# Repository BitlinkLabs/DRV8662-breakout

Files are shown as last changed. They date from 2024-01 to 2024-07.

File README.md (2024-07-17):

# DRV8662-breakout

<p align="center">
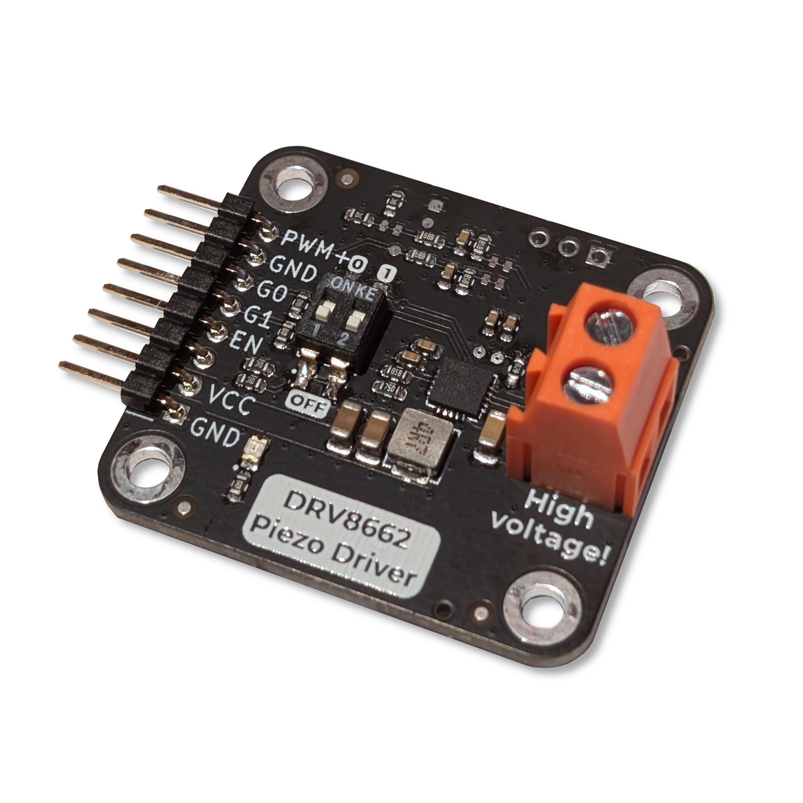
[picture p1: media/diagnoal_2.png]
  
&nbsp; &nbsp; &nbsp; &nbsp;
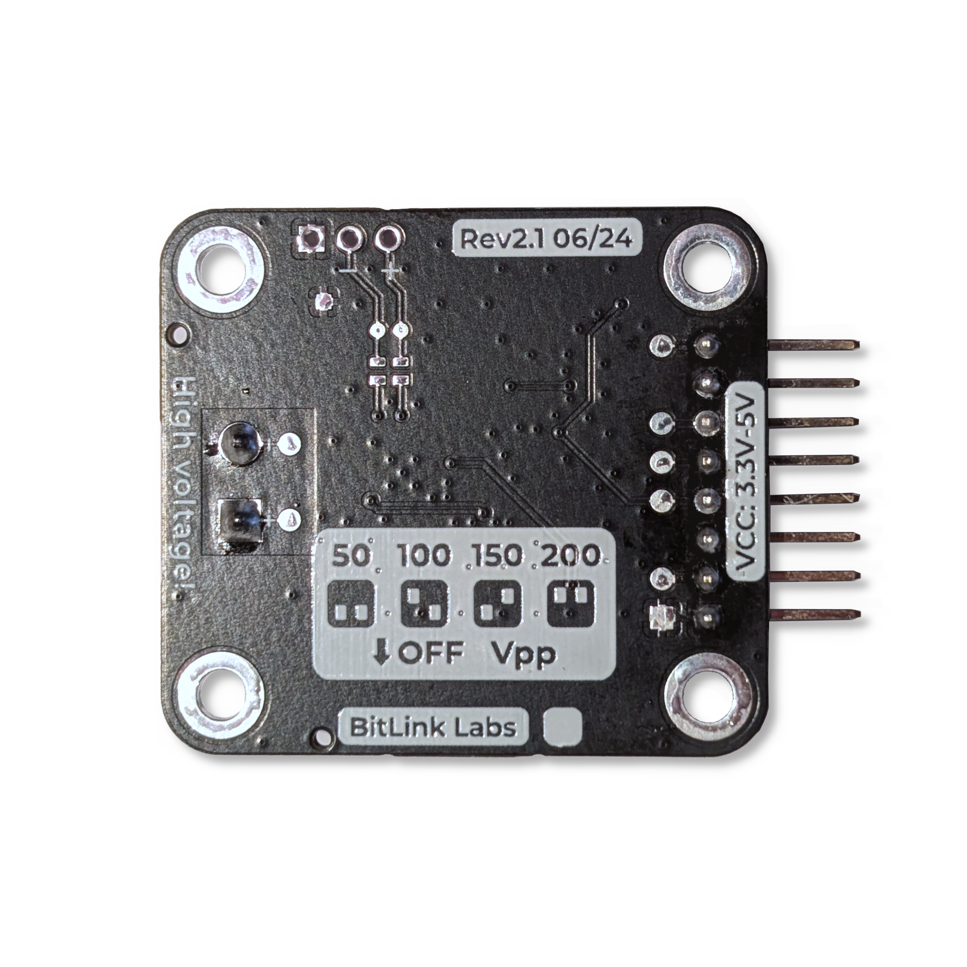
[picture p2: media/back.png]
  
&nbsp; &nbsp; &nbsp; &nbsp;
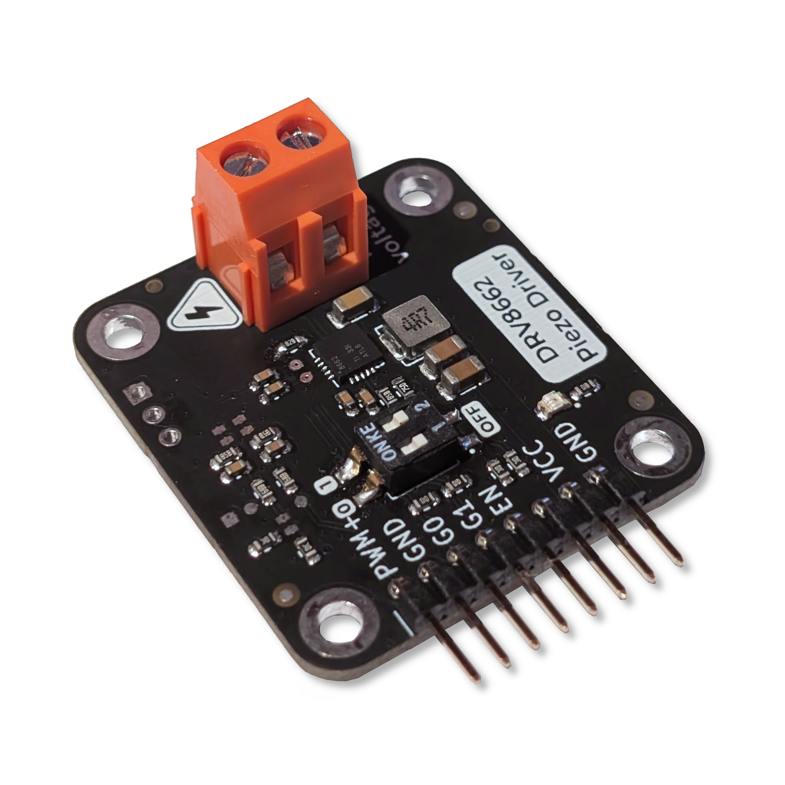
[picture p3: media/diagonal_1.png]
Dark
  
</p>

### What is it?
This is a ready-to-go development board with everything necessary to run piezo actuators.
It features a DRV8662 IC from Texas Instruments and all the additional circuitry for it to work as expected.

### How does it function?
The IC serves multiple purposes. First of all it is a boost-converter to generate up 200V from the 3.3-5V it takes as an input. Secondly it features an amplifier which takes a PWM Signal and drives the Output pins to the respective differential values according to the input.

At the output you can connect a piezo actuator for haptic feedback or valves & pumps.
The output voltage is an AC Waveform with an adjustable Peak-to-Peak voltage.

### What is special about it?
The Output voltage can be to 4 approximate values: 50Vpp, 100Vpp, 150Vpp, 200Vpp using a simple dip switch.

### How do I get started?
All you need to do is connect an PWM and GND pin of a microcontroller to the PWM+ Pin and GND pin of the development board respectively. This covers the “signal” part.
To power the dev board you can either use the USB mini jack (we recommend using a USB hub for this) or through the included VCC and GND Pins. 
Be sure to stick to an input voltage of 3.3V to 5V and be aware that the USB voltage will be present on the VCC pin.



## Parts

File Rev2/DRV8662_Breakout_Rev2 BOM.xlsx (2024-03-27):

DRV 8662 Breakout Rev2 |  |  |  |  |  |  |  | (Stand 27.03.24)
Ref | Description | Qnty | Value | Cmp name | Footprint | VoltageRating | ManuNumber | LCSC Part Number | Stock | Link | Datasheet
C1, C2, C5, C6, C7, C8, |  | 6 | 100nF | C_Small | Capacitor_SMD:C_0603_1608Metric |  |  | C14663 | At home | https://jlcpcb.com/partdetail/Yageo-CC0603KRX7R9BB104/C14663 | ~
C3, | 250V Boost cap. | 1 | 100nF | C_Small | Capacitor_SMD:C_1206_3216Metric |  |  | C346235 |  | https://www.lcsc.com/product-detail/Multilayer-Ceramic-Capacitors-MLCC-SMD-SMT_Samsung-Electro-Mechanics-CL31B104KEHNNNE_C346235.html | ~
C9, C10, |  | 2 | 10uF | C | Capacitor_SMD:C_1206_3216Metric |  |  | C13585 |  | https://www.lcsc.com/product-detail/Multilayer-Ceramic-Capacitors-MLCC-SMD-SMT_Samsung-Electro-Mechanics-CL31A106KBHNNNE_C13585.html | ~
D1, |  | 1 | LED_Small | LED_Small | LED_SMD:LED_0805_2012Metric |  |  |  | At home |  | ~
J1, |  | 1 | Conn_IO | Conn_01x08 | MAINTECH_Connectors:PinHeader_1x08_P2.54mm_Horizontal_withSmdPads |  |  |  | At home |  | ~
J2, | Orange screw terminal | 1 | Conn_Screw | Screw_Terminal_01x02 | MAINTECH_Connectors:DB128L-5.08-2P |  |  | C430603 |  | https://www.lcsc.com/product-detail/Screw-terminal_DORABO-DB128L-5-08-2P-OG-S_C430603.html | ~
L1, | Inductor | 1 | 4.7uH | L | MAINTECH_Passives:Inductor_FXL0420-4R7-M |  | FXL0420-4R7-M | C167208 |  | https://www.lcsc.com/product-detail/Power-Inductors_cjiang-Changjiang-Microelectronics-Tech-FXL0420-4R7-M_C167208.html | ~
R1, R6, R7, R16, |  | 4 | 10k | R_Small | Resistor_SMD:R_0603_1608Metric |  |  | C25804 | At home | https://jlcpcb.com/partdetail/26547-0603WAF1002T5E/C25804 | ~
R14, R15, |  | 2 | 100k | R_Small | Resistor_SMD:R_0603_1608Metric
R2, |  | 1 | 6.98k | R_Small | Resistor_SMD:R_0603_1608Metric_Pad0.98x0.95mm_HandSolder |  |  | C862806 |  | https://www.lcsc.com/product-detail/Chip-Resistor-Surface-Mount_YAGEO-RT0603DRD076K98L_C862806.html | ~
R3, |  | 1 | 590k | R_Small | Resistor_SMD:R_0603_1608Metric_Pad0.98x0.95mm_HandSolder |  |  | C185318 |  | https://www.lcsc.com/product-detail/Chip-Resistor-Surface-Mount_YAGEO-RC0603FR-07590KL_C185318.html | ~
R4, |  | 1 | 7.5k | R_Small | Resistor_SMD:R_0603_1608Metric_Pad0.98x0.95mm_HandSolder |  |  | C23234 |  | https://www.lcsc.com/product-detail/Chip-Resistor-Surface-Mount_UNI-ROYAL-Uniroyal-Elec-0603WAF7501T5E_C23234.html | ~
R5, R9, |  | 2 | 4.99k | R_Small | Resistor_SMD:R_0603_1608Metric |  |  | C23046 |  | https://www.lcsc.com/product-detail/Chip-Resistor-Surface-Mount_UNI-ROYAL-Uniroyal-Elec-0603WAF4991T5E_C23046.html | ~
R8, R12, R13, |  | 3 | 0R | R_Small | Resistor_SMD:R_0603_1608Metric_Pad0.98x0.95mm_HandSolder |  |  | C21189 |  | https://www.lcsc.com/product-detail/Chip-Resistor-Surface-Mount_UNI-ROYAL-Uniroyal-Elec-0603WAF0000T5E_C21189.html | ~
R10, R11, | FB & Filter Resistor | 2 | 7.5k | R_Small | Resistor_SMD:R_0603_1608Metric |  |  | C23234 |  | https://www.lcsc.com/product-detail/Chip-Resistor-Surface-Mount_UNI-ROYAL-Uniroyal-Elec-0603WAF7501T5E_C23234.html | ~
R19, |  | 1 | 1k | R_Small | Resistor_SMD:R_0603_1608Metric |  |  |  | At home |  | ~
SW1, | Dip switch | 1 | SW_Gain | SW_DIP_x02 | MAINTECH_mechanical:SW_DIP_x02_P2.54_W5.08_C6709488 |  | 2.54-2P TPPT | C6709488 |  | https://www.lcsc.com/product-detail/DIP-Switches_SHOU-HAN-2-54-2P-TPPT_C6709488.html | ~
U1, | DRB8662 IC | 1 | DRV8662 | DRV8662 | Package_DFN_QFN:Texas_S-PVQFN-N20_EP2.7x2.7mm_ThermalVias |  |  | C181554 |  | https://www.lcsc.com/product-detail/Motor-Driver-ICs_Texas-Instruments-DRV8662RGPT_C181554.html | http://www.ti.com/lit/ds/symlink/drv8662.pdf

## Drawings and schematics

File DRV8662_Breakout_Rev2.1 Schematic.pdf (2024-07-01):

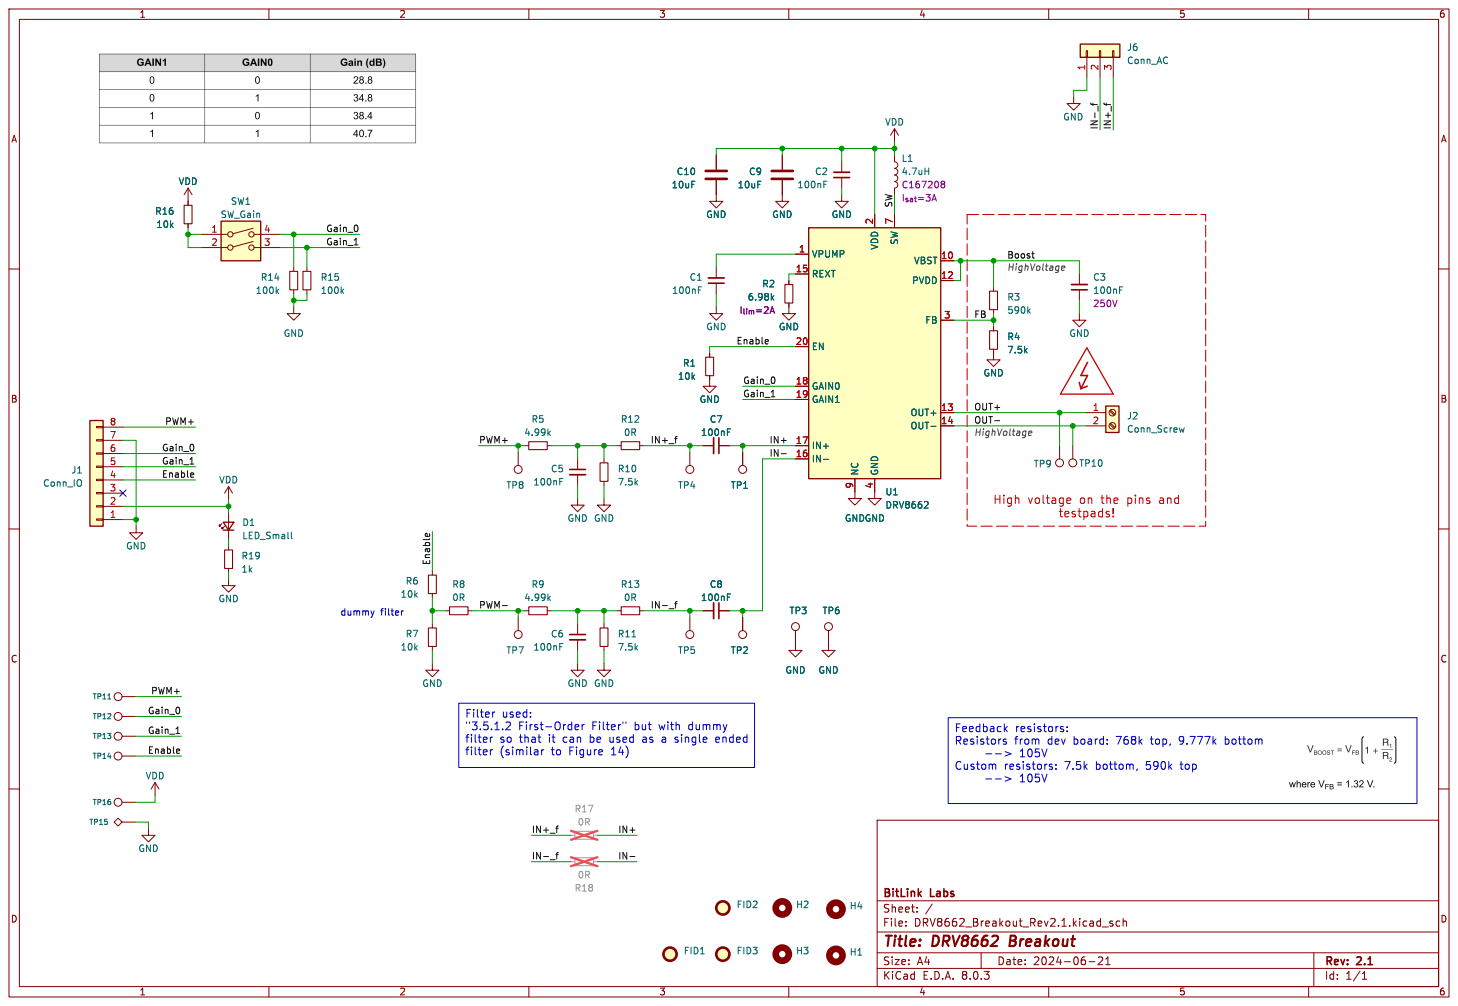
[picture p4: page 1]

filter so that it can be used as a single ended

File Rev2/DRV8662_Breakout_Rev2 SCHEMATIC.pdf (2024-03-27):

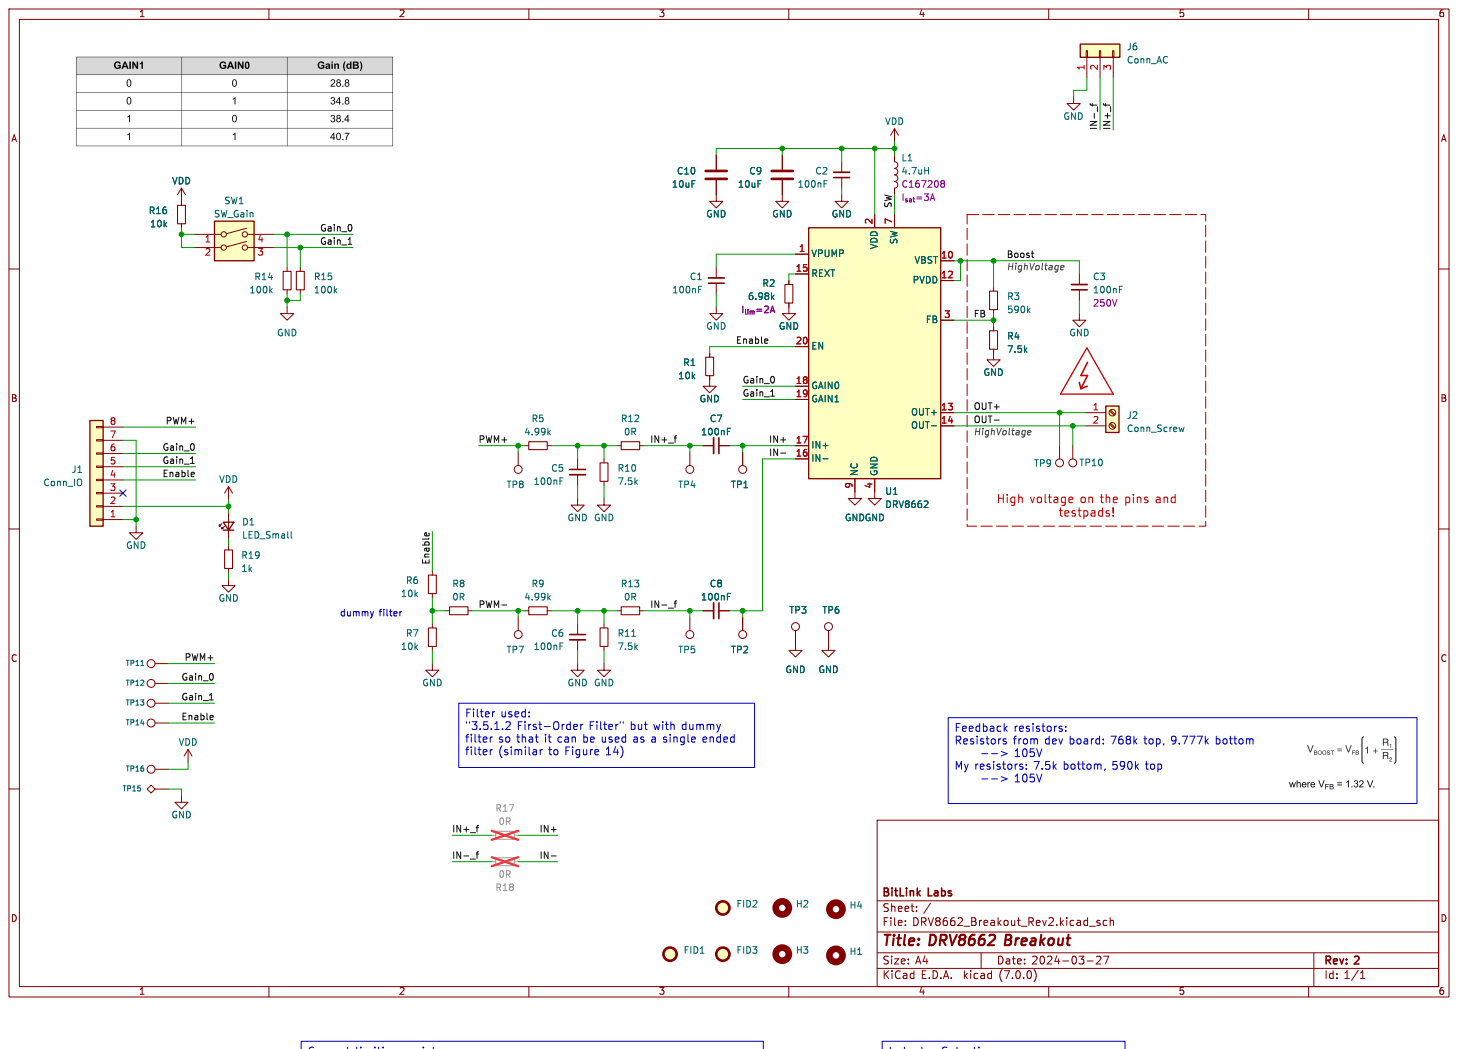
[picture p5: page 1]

testpads! Feedback resistors: Resistors from dev board: 768k top, 9.777k bottom

High voltage on the pins and

filter so that it can be used as a single ended

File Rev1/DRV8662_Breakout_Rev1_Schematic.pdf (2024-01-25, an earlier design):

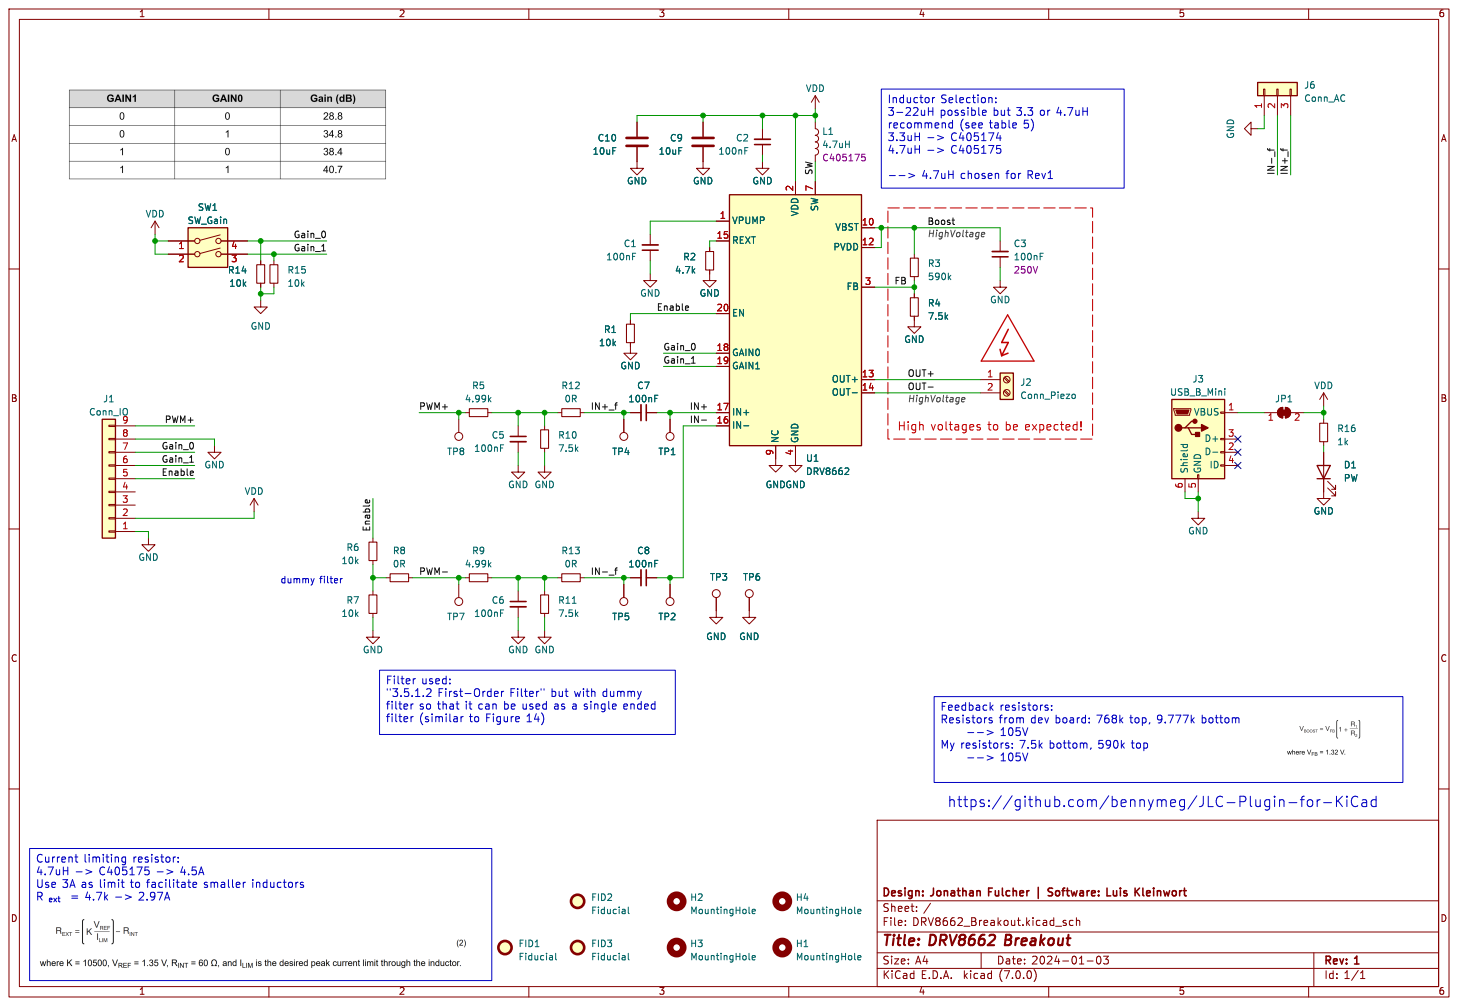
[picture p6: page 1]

filter so that it can be used as a single ended

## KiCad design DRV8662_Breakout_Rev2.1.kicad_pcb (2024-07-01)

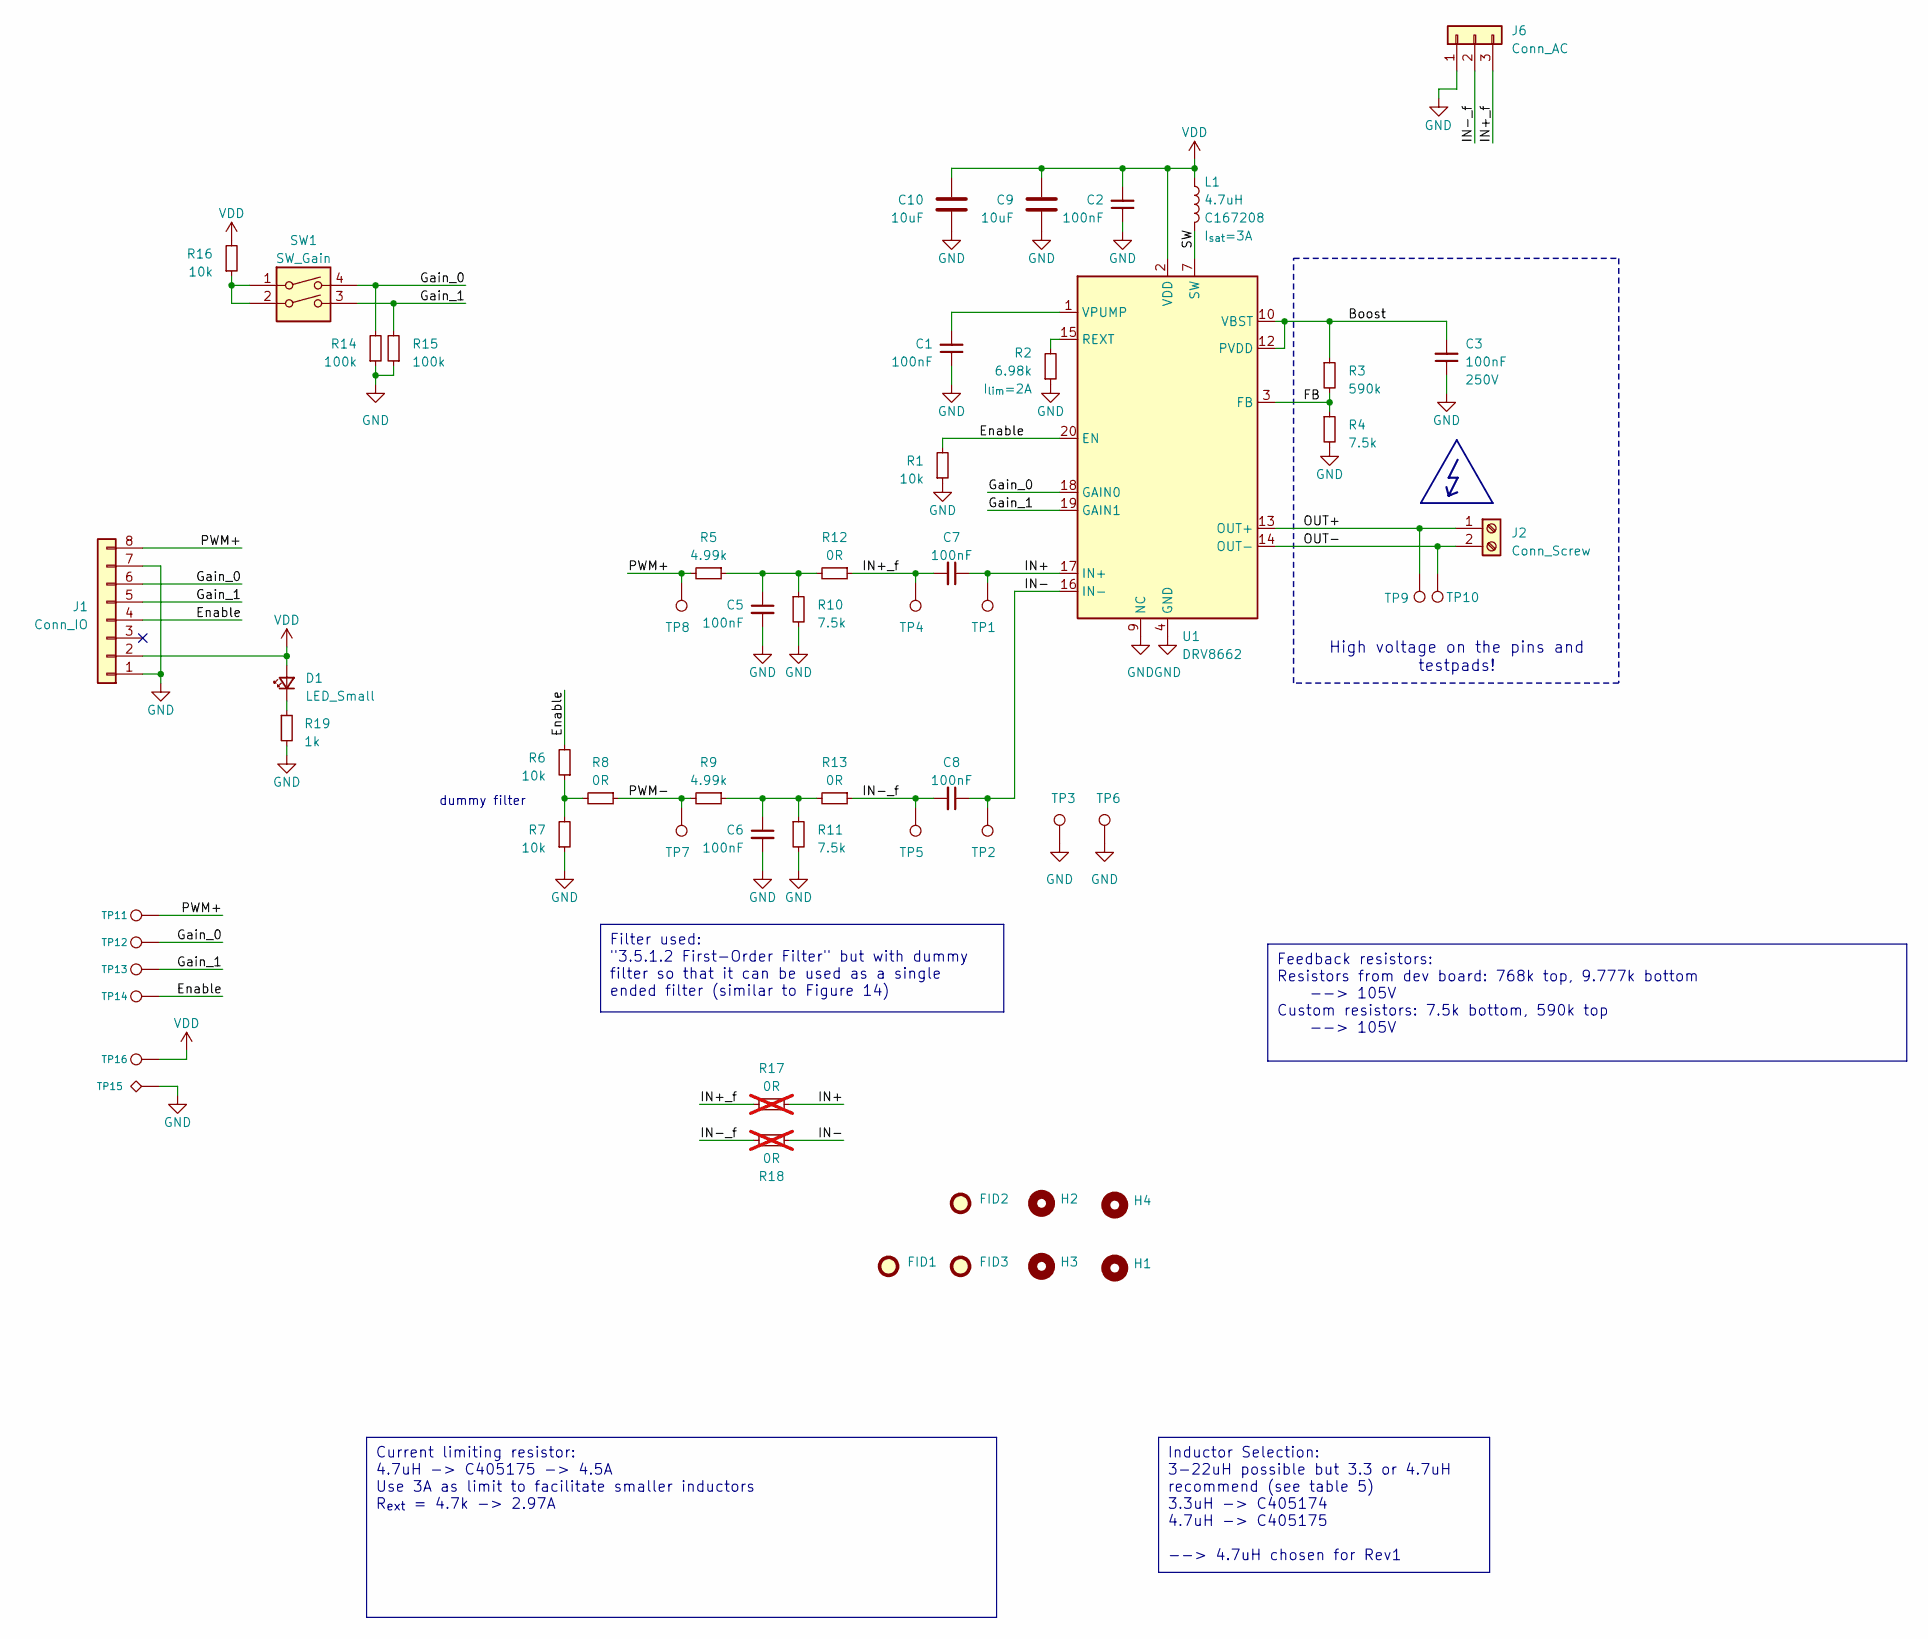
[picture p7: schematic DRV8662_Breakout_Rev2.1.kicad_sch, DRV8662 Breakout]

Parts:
C1, C2, C5, C6, C7, C8: 100nF; C_0603_1608Metric; PartNumber C14663; LCSC Part # C14663
C3: 100nF; C_1206_3216Metric; Voltage 250V; PartNumber C346235; LCSC Part # C346235
C9, C10: 10uF; C_1206_3216Metric; PartNumber C13585; LCSC Part # C13585
D1: LED_Small; LED_0805_2012Metric; LCSC Part # C84256
FID1, FID2, FID3: Fiducial; Fiducial_standart
H1, H2, H3, H4: MountingHole; MountingHole_3.2mm_M3_ISO7380_Pad_TopBottom
J1: Conn_IO; PinHeader_1x08_P2.54mm_Horizontal_withSmdPads
J2: Conn_Screw; DB128L-5.08-2P; PartNumber C430603; LCSC Part # C430603
J6: Conn_AC; PinHeader_1x03_P2.54mm_Vertical
L1: 4.7uH; Inductor_FXL0420-4R7-M; PartNumber C167208; LCSC Part # C167208
R1, R6, R7, R16: 10k; R_0603_1608Metric; PartNumber C25804; LCSC Part # C25804
R2: 6.98k; R_0603_1608Metric_Pad0.98x0.95mm_HandSolder; PartNumber C862806; LCSC Part # C862806
R3: 590k; R_0603_1608Metric_Pad0.98x0.95mm_HandSolder; PartNumber C185318; LCSC Part # C185318
R4, R10, R11: 7.5k; R_0603_1608Metric; PartNumber C23234; LCSC Part # C23234
R5, R9: 4.99k; R_0603_1608Metric; PartNumber C23046; LCSC Part # C23046
R8, R12, R13: 0R; Jumper_Small-2_bridged; PartNumber C21189
R14, R15: 100k; R_0603_1608Metric; LCSC Part # C25803
R17, R18: 0R; Jumper_Small-2_open; PartNumber C21189; not fitted
R19: 1k; R_0603_1608Metric; LCSC Part # C21190
SW1: SW_Gain; SW_DIP_x02_P2.54_W5.08_C6709488; PartNumber C6709488; LCSC Part # C6709488
TP1, TP2, TP4, TP5, TP7, TP8: TestPoint; TestPoint_Pad_D1.0mm_NoSilk
TP3, TP6: TestPoint; TestPoint_Pad_1.0x1.0mm
TP9, TP10, TP11, TP12, TP13, TP14, TP16: TestPoint; TestPoint_Pad_D1.5mm_NoSilk
TP15: TestPoint_Alt; TestPoint_Pad_1.5x1.5mm
U1: DRV8662; Texas_S-PVQFN-N20_EP2.7x2.7mm_ThermalVias; PartNumber C181554; LCSC Part # C181554

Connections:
/Boost: C3.2, R3.1, U1.10 (VBST), U1.11 (VBST), U1.12 (PVDD)
/Enable: J1.4, R1.2, R6.2, TP14.1, U1.20 (EN)
/FB: R3.2, R4.1, U1.3 (FB)
/Gain_0: J1.6, R14.2, SW1.4, TP12.1, U1.18 (GAIN0)
/Gain_1: J1.5, R15.2, SW1.3, TP13.1, U1.19 (GAIN1)
/IN+: C7.1, R17.1, TP1.1, U1.17 (IN+)
/IN+_f: C7.2, J6.3, R12.1, R17.2, TP4.1
/IN-: C8.1, R18.1, TP2.1, U1.16 (IN-)
/IN-_f: C8.2, J6.2, R13.1, R18.2, TP5.1
/OUT+: J2.1, TP9.1, U1.13 (OUT+)
/OUT-: J2.2, TP10.1, U1.14 (OUT-)
/PWM+: J1.8, R5.2, TP8.1, TP11.1
/PWM-: R8.1, R9.2, TP7.1
/SW: L1.2, U1.7 (SW), U1.8 (SW)
GND: C1.1, C2.1, C3.1, C5.2, C6.2, C9.2, C10.2, J1.1, J1.7, J6.1, R1.1, R2.1, R4.2, R7.1, R10.2, R11.2, R14.1, R15.1, R19.2, TP3.1, TP6.1, TP15.1, U1.4 (GND), U1.5 (GND), U1.6 (GND), U1.9 (NC), U1.21 (GND)
unnamed: C5.1, R5.1, R10.1, R12.2
unnamed: C6.1, R9.1, R11.1, R13.2
unnamed: D1.1 (K), R19.1
unnamed: R6.1, R7.2, R8.2
unnamed: R16.1, SW1.1, SW1.2
unnamed: R2.2, U1.15 (REXT)
unnamed: C1.2, U1.1 (VPUMP)
VDD: C2.2, C9.1, C10.1, D1.2 (A), J1.2, L1.1, R16.2, TP16.1, U1.2 (VDD)

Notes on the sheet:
Current limiting resistor: 4.7uH -> C405175 -> 4.5A Use 3A as limit to facilitate smaller inductors R_{ext} = 4.7k -> 2.97A
Filter used: "3.5.1.2 First-Order Filter" but with dummy filter so that it can be used as a single ended filter (similar to Figure 14)
Feedback resistors: Resistors from dev board: 768k top, 9.777k bottom --> 105V Custom resistors: 7.5k bottom, 590k top --> 105V
High voltage on the pins and testpads!
Inductor Selection: 3-22uH possible but 3.3 or 4.7uH recommend (see table 5) 3.3uH -> C405174 4.7uH -> C405175 --> 4.7uH chosen for Rev1
dummy filter

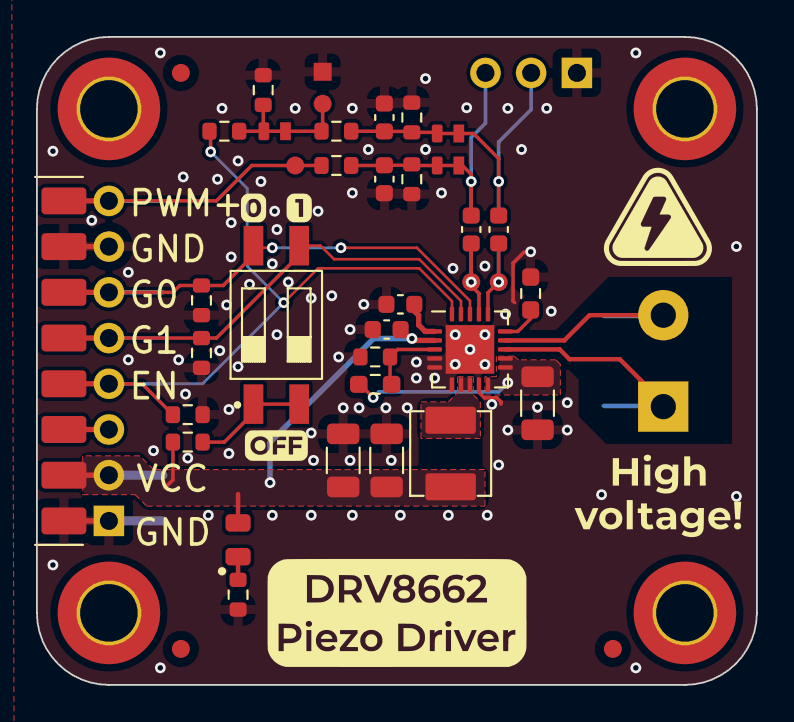
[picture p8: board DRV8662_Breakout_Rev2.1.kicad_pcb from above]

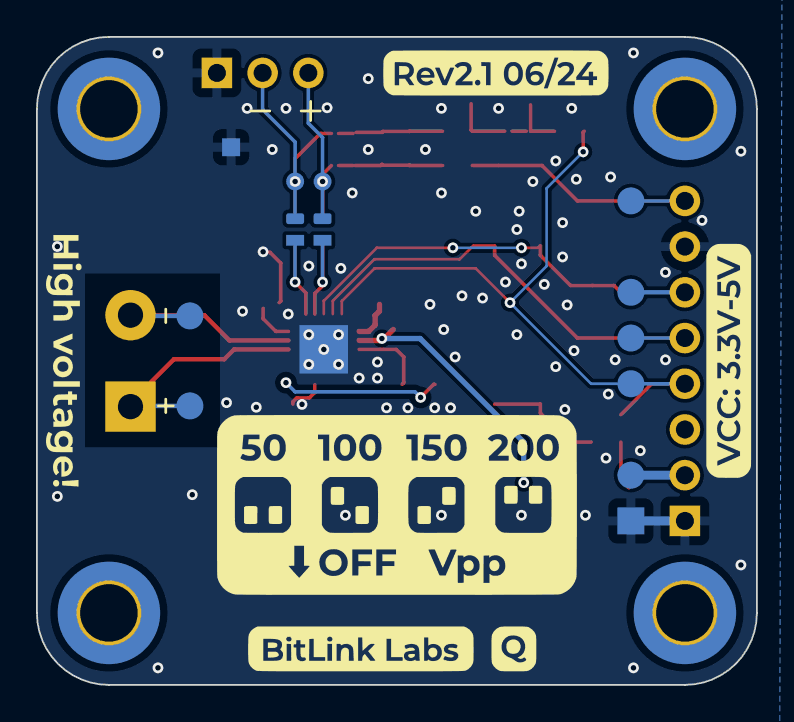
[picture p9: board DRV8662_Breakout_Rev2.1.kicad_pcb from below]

Board: 2 copper layers, 40.0 x 36.0 mm, 58 parts (13 on the bottom side), 23 nets.

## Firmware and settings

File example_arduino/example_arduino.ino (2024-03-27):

/*

This example shows how to use DRV8662 piezo driver.
This code was tested using an ESP32.

*/

#define DRV8662_ENABLE_PIN 32
#define DRV8662_PWM_PN 33

#define NUM_PWM_BITS 9
#define PWM_FREQUENCY 100 * 1000


#define FULL_RANGE ((1 << NUM_PWM_BITS) - 1)
#define HALF_RANGE (FULL_RANGE / 2)

void setup() {
  Serial.begin(115200);
  Serial.println("You can update the frequency with the serial monitor");

  ledcSetup(0, 100 * 1000, NUM_PWM_BITS);
  ledcAttachPin(DRV8662_PWM_PN, 0);
  pinMode(DRV8662_ENABLE_PIN, OUTPUT);

  digitalWrite(DRV8662_ENABLE_PIN, LOW);
  ledcWrite(0, HALF_RANGE);
  delay(100);

  digitalWrite(DRV8662_ENABLE_PIN, HIGH);
  delay(100);
}

int setFrequency = 120;

void drivePiezo(
  float frequency,
  int durationMs
) {

  ledcWrite(0, HALF_RANGE);
  time_t startUs = micros();
  time_t deltaTus = 0;
  do {
    deltaTus = micros() - startUs;

    int pwm =
        HALF_RANGE +
        sin(deltaTus * frequency / 1000000.0f * TWO_PI) * HALF_RANGE;
        ledcWrite(0, pwm);
        delayMicroseconds(10);

  } while (deltaTus < durationMs * 1000);

  ledcWrite(0, HALF_RANGE);
}

void readFrequencyFromSerial();

void loop() {
  readFrequencyFromSerial();

  drivePiezo(
    setFrequency,
    50
  );

  delay(500);
  readFrequencyFromSerial();

  drivePiezo(
    setFrequency,
    100
  );

  delay(500);
  readFrequencyFromSerial();

  drivePiezo(
    setFrequency,
    200
  );

  delay(500);
  readFrequencyFromSerial();

  drivePiezo(
    setFrequency,
    500
  );

  delay(500);
}



void readFrequencyFromSerial() {

  int temp = Serial.parseInt();
  if (temp > 0) {
    setFrequency = temp;
  }
  Serial.print("Using frequency: ");
  Serial.println(setFrequency);
}

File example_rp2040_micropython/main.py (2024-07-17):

import math
import time

import rp2
from machine import Pin, PWM

PWM_FREQ = 125_000
PWM_PLUS_PIN = 9
EN_PIN = 12

U16_MAX = 0xFFFF

pwm_plus = PWM(Pin(PWM_PLUS_PIN))
pwm_plus.init(freq=PWM_FREQ, duty_u16=int(U16_MAX * 0.5))

en = Pin(EN_PIN, Pin.OUT)


def reset_drv():
    en.value(0)
    set_output(0)
    time.sleep(0.1)
    en.value(1)
    time.sleep(0.1)


def set_output(out: float):
    """
    :param out: -1 to 1
    """
    pwm_plus.duty_u16(max(0, min(U16_MAX, int((out / 2 + 0.5) * U16_MAX))))


def wait_for_button_press():
    while rp2.bootsel_button() == 0:
        pass


def test_sine_signal(duration, frequency):
    reset_drv()

    start_time = time.ticks_us()

    dt = 0
    while dt < duration:
        dt = time.ticks_diff(time.ticks_us(), start_time) / 1000_000.0
        set_output(math.sin(dt * 2 * math.pi * frequency))

    en.value(0)


print("0")
wait_for_button_press()

time.sleep(1)

while True:
    wait_for_button_press()
    test_sine_signal(1, 100)

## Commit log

2024-01-25 Added Schematic PDF
2024-01-25 Added PDF Schematic
2024-02-10 Add Arduino example
2024-03-27 Added Rev2 design data and moved Rev1 Schematic to /Rev1
    [DRV8662_Breakout_Rev2 BOM.xlsx, DRV8662_Breakout_Rev2.kicad_pcb, DRV8662_Breakout_Rev2.kicad_sch]
2024-07-01 Added Rev2.1 and moved Rev2 into separate folder. Added new Rev2.1 Images.
    [DRV8662_Breakout_Rev2 BOM.xlsx, DRV8662_Breakout_Rev2.1.kicad_pcb, DRV8662_Breakout_Rev2.1.kicad_sch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]
